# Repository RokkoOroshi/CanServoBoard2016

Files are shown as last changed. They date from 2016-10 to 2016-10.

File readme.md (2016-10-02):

# CAN Servo Driver Board

can通信機能対応サーボ制御基板

## License

- MIT

## 使用ライブラリ等

- Adafruit-PWM-Servo-Driver-Library : BSD : https://github.com/adafruit/Adafruit-PWM-Servo-Driver-Library
- CAN_BUS_Shield : MIT : https://github.com/Seeed-Studio/CAN_BUS_Shield
- MsTimer2 : LGPL : http://playground.arduino.cc/Main/MsTimer2
- pins_arduino.h : LGPL
- Arduino-SerialCommand : ? : https://github.com/kroimon/Arduino-SerialCommand

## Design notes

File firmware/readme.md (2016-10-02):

# CAN Servo Board Firmware

## Arduino IDE での使用方法
1. Arduino IDEをダウンロード・インストール
2. install.batを管理者として実行（Arduino IDEのフォルダ下に必要なファイルのシンボリックリンクを作ってる）
3. Arduino IDEのボード選択メニューで"RokkoOroshiCanServoBoard"を選択

これで各ピンのシンボルが自動で定義され、各種ライブラリをincludeできるようになる。

また、この基板はArduinoProMini互換であるが、ブートローダーは書き込み速度を通常より高速にしたものを使用しているため、IDEでArduinoProMiniを選択した場合書き込みできないので注意。

## ライブラリ
Arduino IDEのメニュー include library から選択できるようになっているはず。

現状、依存ライブラリをメインのファイル内でincludeしないとコンパイルエラーになる

### CanCommunication

* CAN上で各ノードが相互に通信するためのライブラリ
* 通信規格は独自の簡易的なものを使用、詳細はcan_communication_def.h参照
* SPI.h(標準ライブラリ), mcp_can.h(CAN_BUS_SHEILDライブラリ) に依存

## PWM出力を使う
* PWM出力は外部のIC(PCA9685)が行う
* 基本的に　https://www.switch-science.com/catalog/961/と同じ感じにしている
* Arduinoから使うライブラリが作られているので利用。使い方はそのライブラリを参照。
* サーボ用電源出力をOFFにするピンも搭載している

## IOポートを使う
* Arduino の A0,A1,A2,A3, D9,D10に当たるポートを搭載しているのでその部分はArudinoと同じように使える

## その他
* このフォルダ下にhardware_profile.h, can_communication_dfe.hがあるが、これは内容確認用に置いているだけ。RokkoOroshiCanServoBoard下の深いところに同じファイルがあり、ArduinoIDEではそちらを参照している。このフォルダ下のものは最新でない可能性があるので注意。
* ピン配置はhardware_profile.hを見ると早い
* can_communication_defには通信規格を書いている

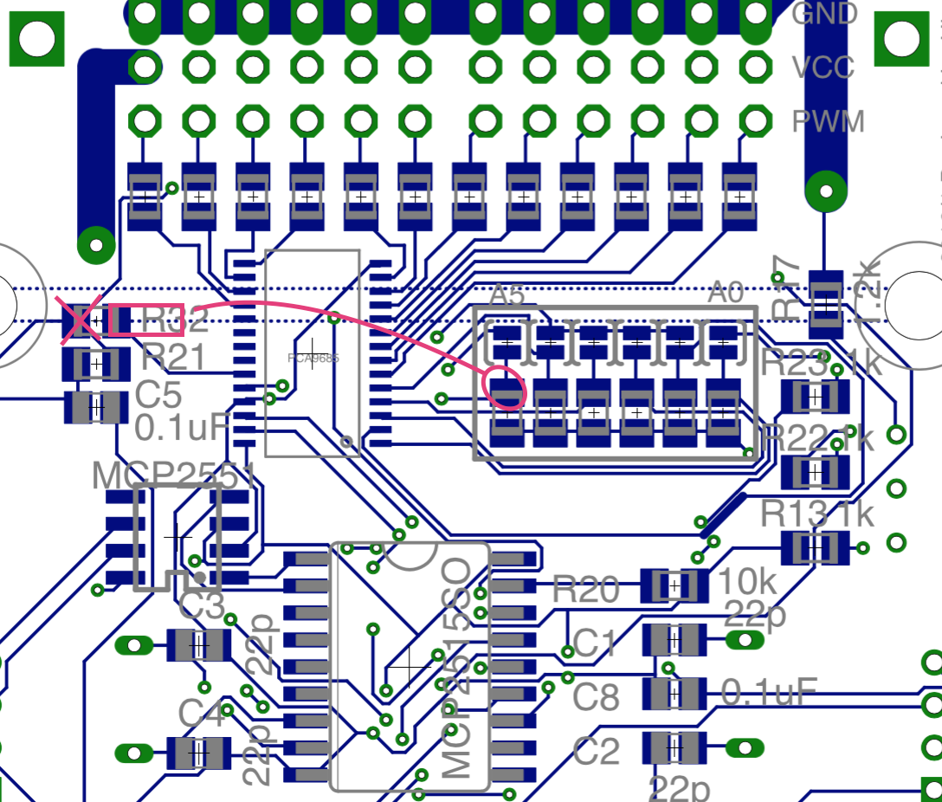
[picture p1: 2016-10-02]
hardware/基板修正箇所２.png

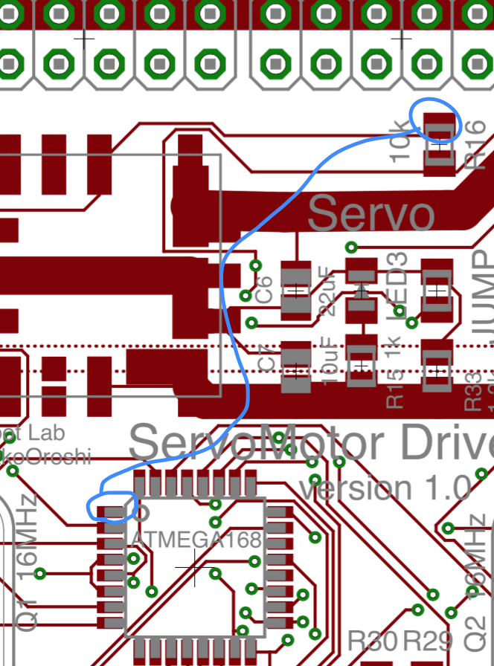
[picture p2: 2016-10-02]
hardware/基板修正箇所１.png

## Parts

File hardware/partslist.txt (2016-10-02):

抵抗

PWM出力部(R1~R12)	330Ω
白枠部(R24~R28,R31)	10kΩ

R13	1k	led
R14	1k	led
R15	1k	led
R16	10k	プルアップ
R17	1.2k	分圧
R18	可変20k
R19	39k	can
R20	10k	リセットプルアップ
R21	10k	リセットプルアップ
R22	1k	led
R23	1k	led
R29	4.7k	I2Cプルアップ
R30	4.7k	I2Cプルアップ
R32	10k
R33	1.2k

コンデンサ
C1~C4	22pF	発信子負荷
C5	0.1uF	DRT
C6	22uF
C7	10uF
C8	0.1uF	パスコン

その他
ATMega328p	1個	メインマイコン
MCP2551		1個	CAN通信
MCP2515		1個	CAN通信
水晶発信器16MHz	2個
チップLED	5個	
B2P-VH		2個	モータ、モータ電源
B4B-ZR		1個	Arduino書き込み、シリアル通信
B6B-ZR		1個	ISP書き込み
B4B-PASK	2個	CAN通信
ピンヘッダ2x3	2個	IO
ピンヘッダ3x12相当		1個	PWM

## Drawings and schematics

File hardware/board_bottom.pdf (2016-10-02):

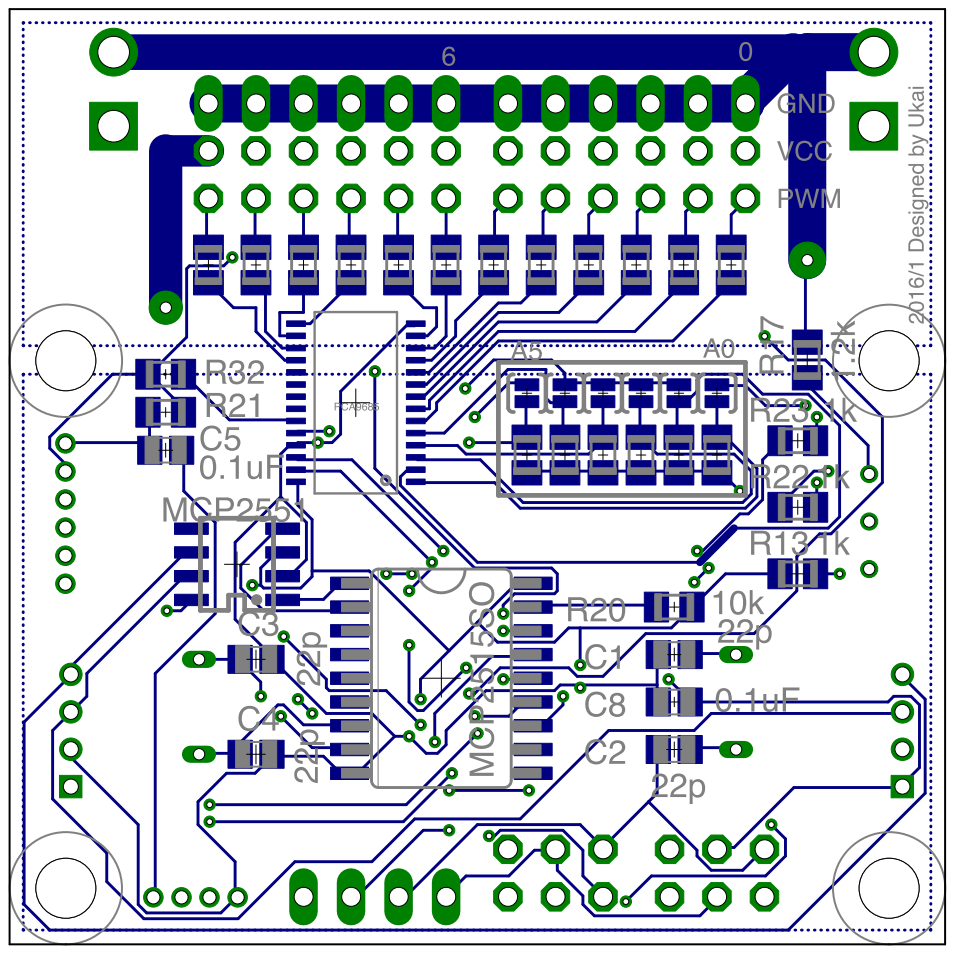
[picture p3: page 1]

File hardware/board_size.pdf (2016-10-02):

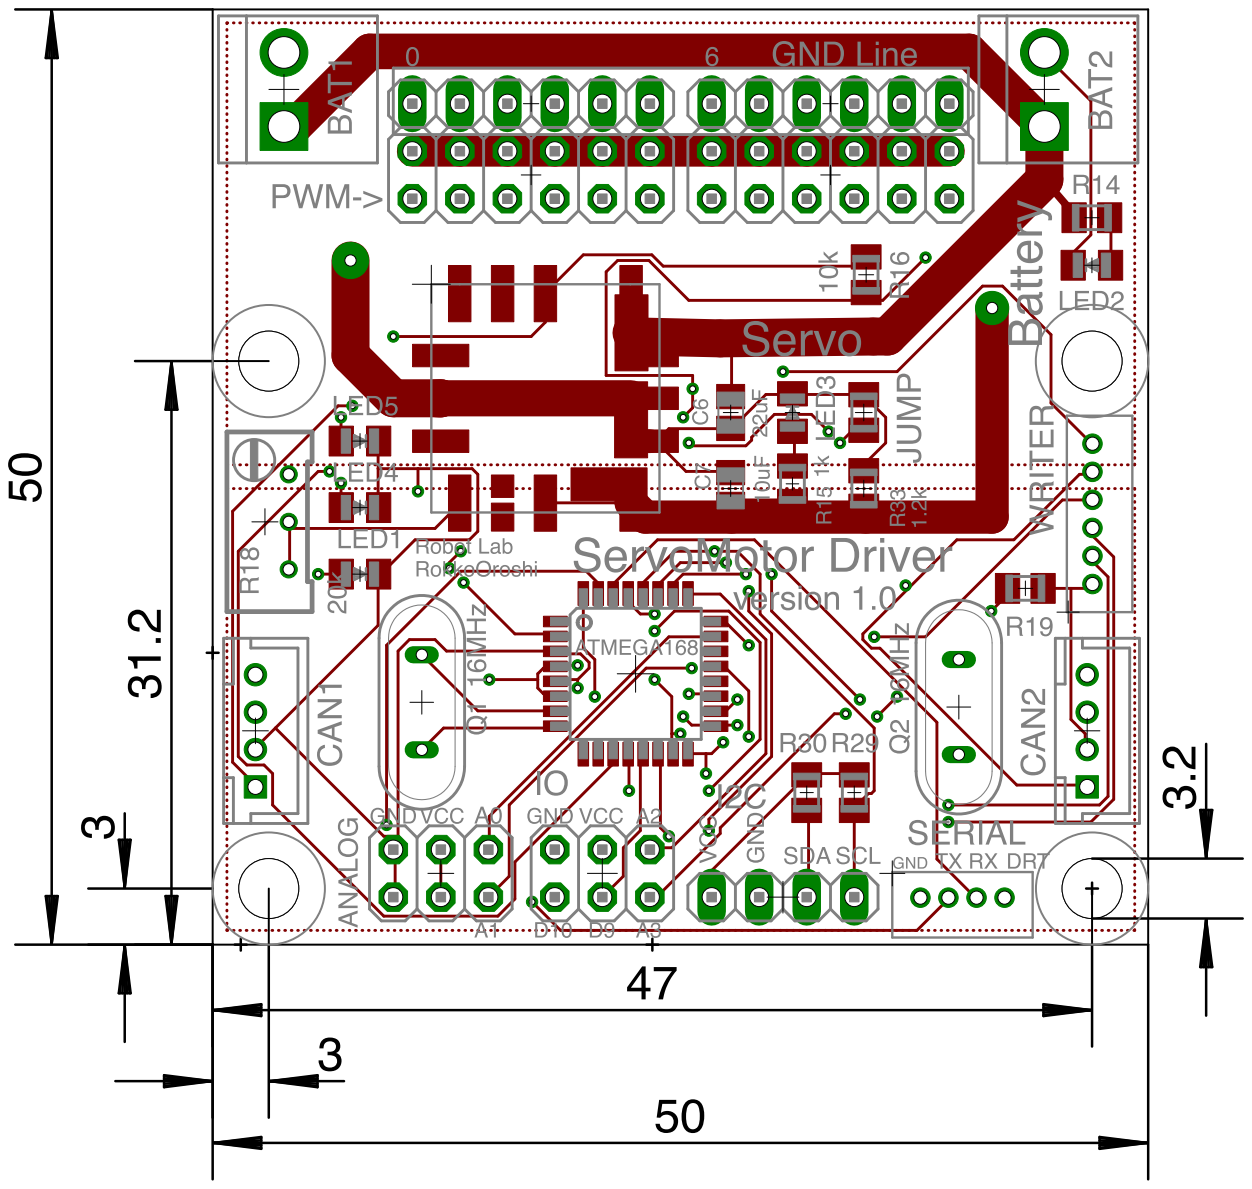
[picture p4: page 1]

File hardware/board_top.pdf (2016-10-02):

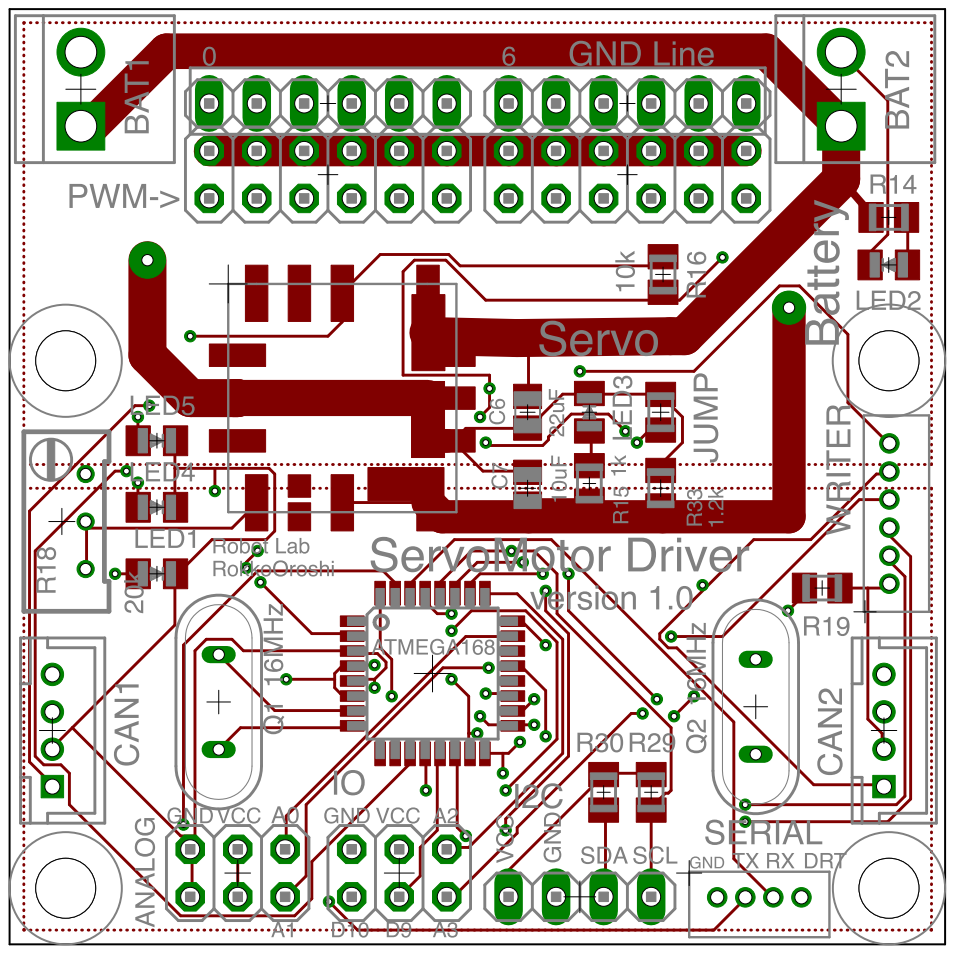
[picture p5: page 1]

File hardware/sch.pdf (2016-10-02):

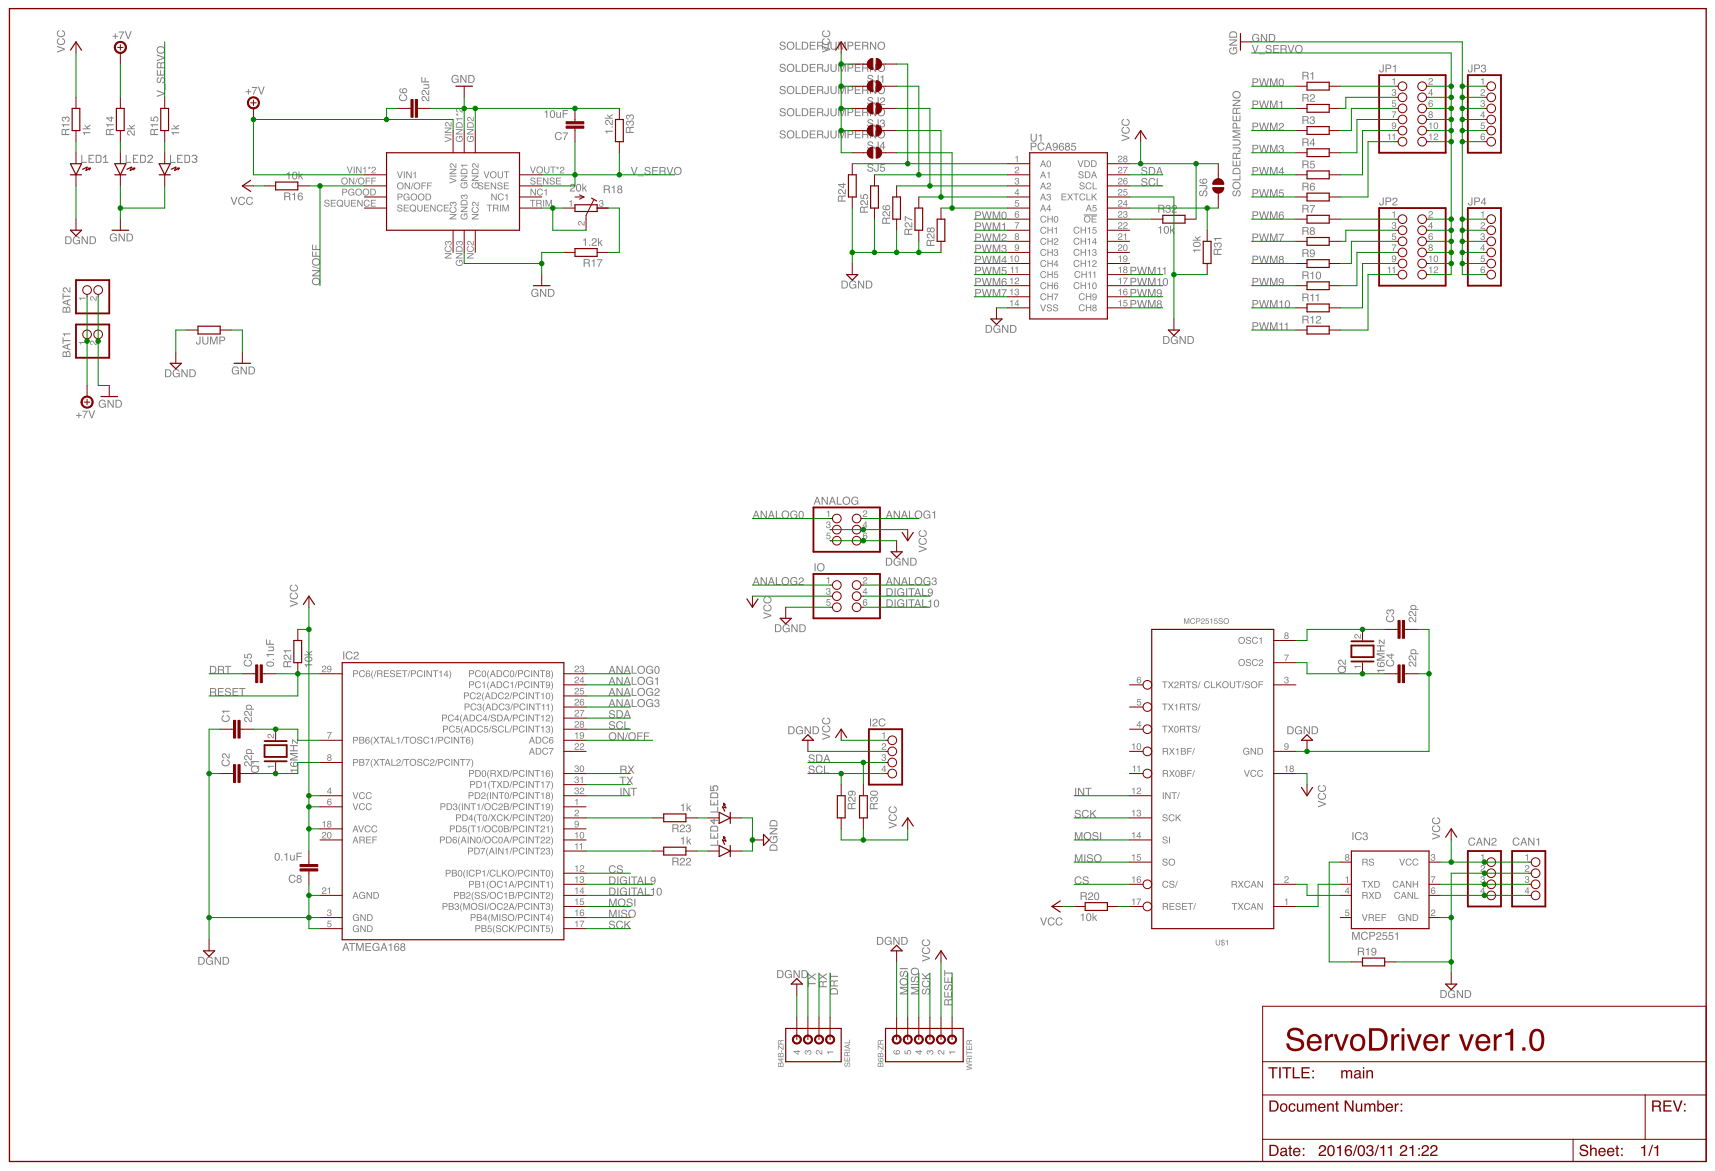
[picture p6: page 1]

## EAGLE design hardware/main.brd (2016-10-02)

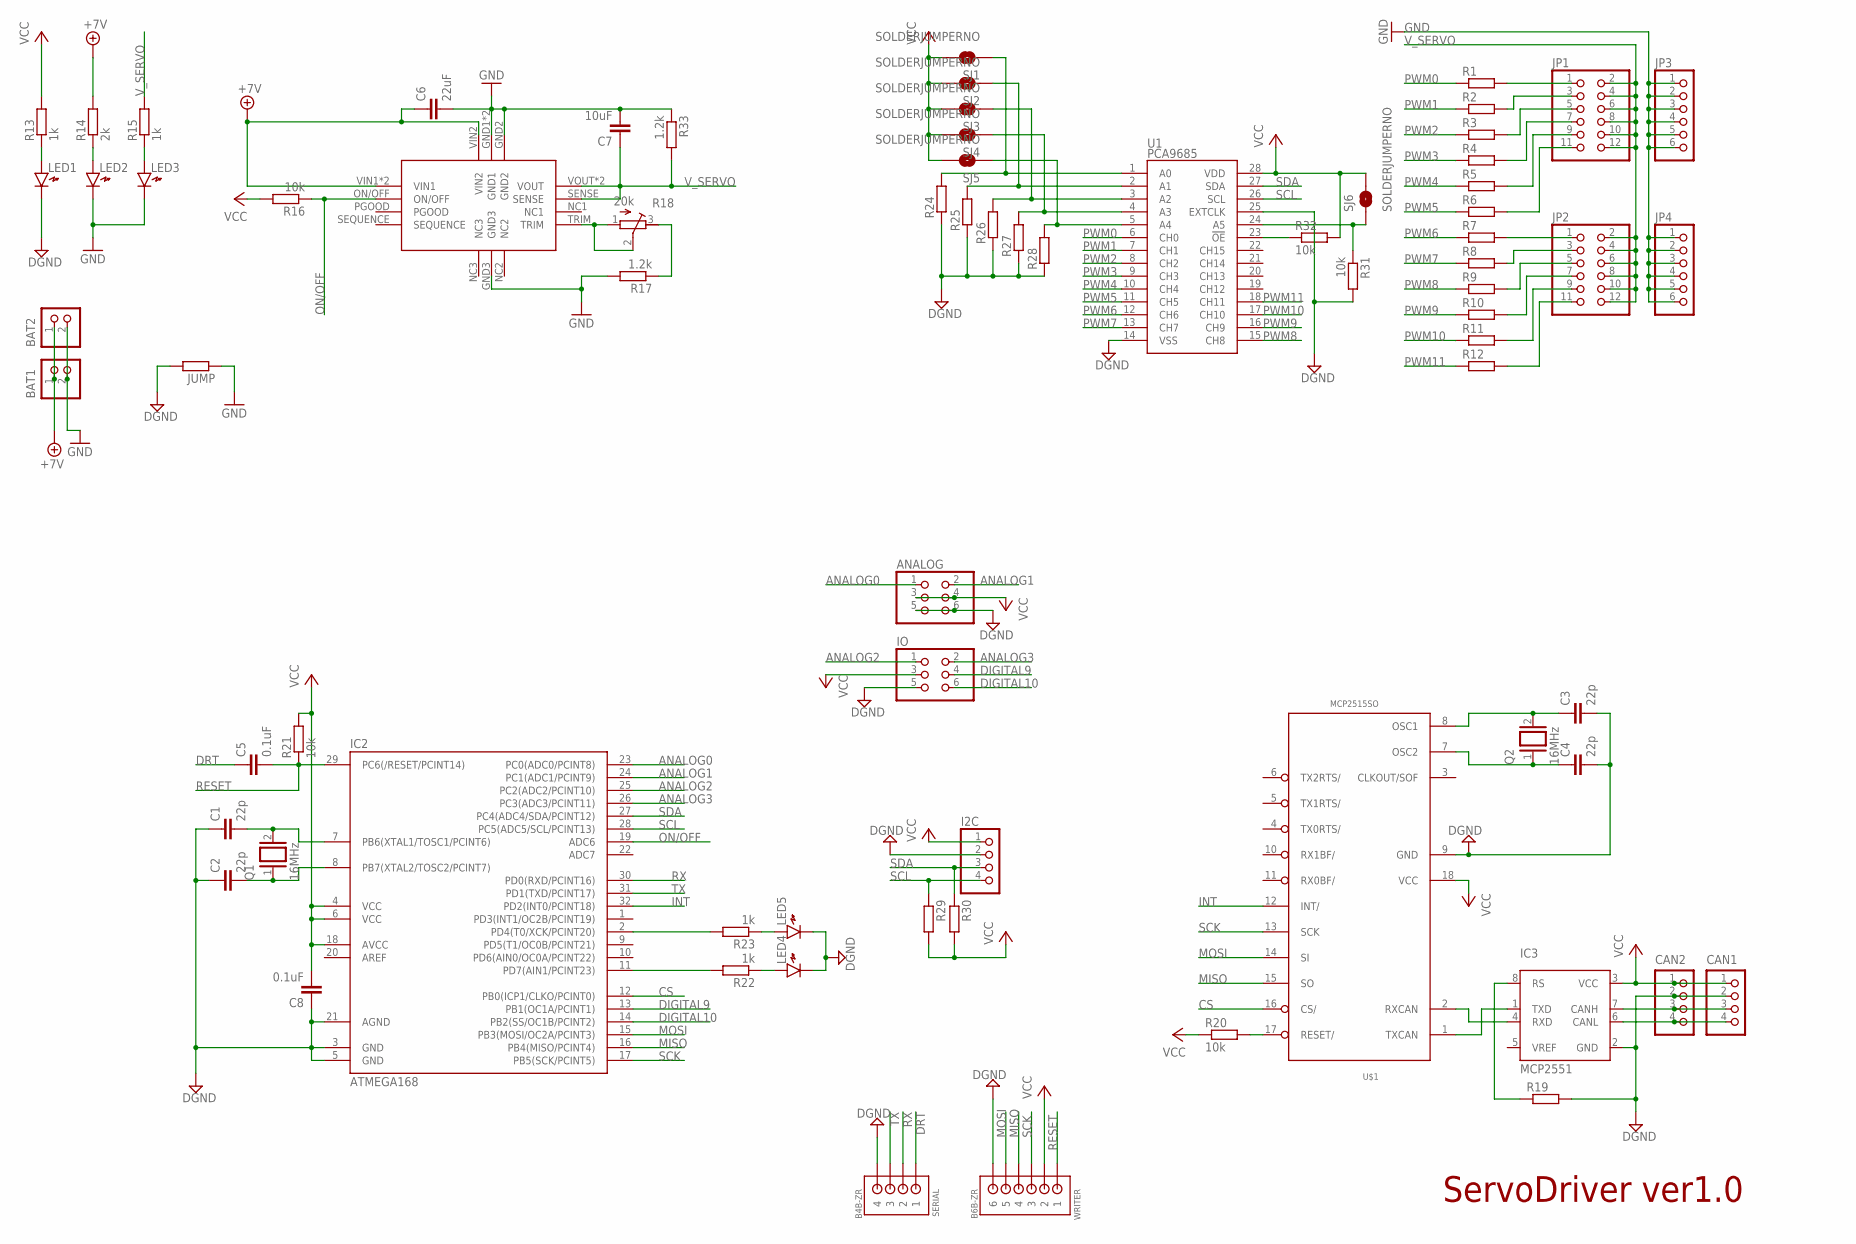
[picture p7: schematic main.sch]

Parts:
ANALOG: PINHD-2X3; 2X03
BAT1, BAT2: B2P-VH
C1, C2, C3, C4: 22p; C2012
C5, C8: 0.1uF; C2012
C6: 22uF; C2012
C7: 10uF; C2012
CAN1, CAN2: B4B-PH-K-S
I2C: PINHD-1X4; 1X04
IC1: OKL-T
IC2: ATMEGA168; TQFP32-08
IC3: MCP2551; SOIC
IO: PINHD-2X3; 2X03
JP1, JP2: PINHD-2X6; 2X06
JP3, JP4: PINHD-1X6; 1X06
JUMP: R-EU_M2012; M2012
LED1, LED2, LED3, LED4, LED5: LED2012
Q1, Q2: 16MHz; QS
R1, R2, R3, R4, R5, R6, R7, R8, R9, R10, R11, R12, R19, R24, R25, R26, R27, R28, R29, R30: R-EU_M2012; M2012
R13, R15, R22, R23: 1k; M2012
R14: 2k; M2012
R16, R20, R21, R31, R32: 10k; M2012
R17, R33: 1.2k; M2012
R18: 20k; RTRIM64W
SERIAL: B4B-ZR
SJ1, SJ2, SJ3, SJ4, SJ5, SJ6: SOLDERJUMPERNO; SJ_2S-NO
U1: PCA9685; TSSOP-28_4MM
U$1: MCP2515SO; SO18L
WRITER: B6B-ZR

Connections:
+7V: BAT1.1, BAT2.1, C6.1, IC1.VIN1, IC1.VIN2, IC1.VIN_BRIDGE (VIN1), R14.2
ANALOG0: ANALOG.1, IC2.23 (PC0(ADC0/PCINT8))
ANALOG1: ANALOG.2, IC2.24 (PC1(ADC1/PCINT9))
ANALOG2: IC2.25 (PC2(ADC2/PCINT10)), IO.1
ANALOG3: IC2.26 (PC3(ADC3/PCINT11)), IO.2
CS: IC2.12 (PB0(ICP1/CLKO/PCINT0)), U$1.16 (CS/)
DGND: ANALOG.5, ANALOG.6, C1.1, C2.1, C3.2, C4.2, C8.1, CAN1.2, CAN2.2, I2C.2, IC2.3 (GND), IC2.5 (GND), IC2.21 (AGND), IC3.2 (GND), IO.5, JUMP.2, LED1.K, LED4.K, LED5.K, R19.2, R24.1, R25.1, R26.1, R27.1, R28.1, R31.2, SERIAL.4, U1.14 (VSS), U1.25 (EXTCLK), U$1.9 (GND), WRITER.6
DIGITAL9: IC2.13 (PB1(OC1A/PCINT1)), IO.4
DIGITAL10: IC2.14 (PB2(SS/OC1B/PCINT2)), IO.6
DRT: C5.1, SERIAL.1
GND: BAT1.2, BAT2.2, C6.2, C7.2, IC1.GND1, IC1.GND2, IC1.GND3, IC1.GND_BRIDGE (GND1), JP3.1, JP3.2, JP3.3, JP3.4, JP3.5, JP3.6, JP4.1, JP4.2, JP4.3, JP4.4, JP4.5, JP4.6, JUMP.1, LED2.K, LED3.K, R17.2, R33.1
INT: IC2.32 (PD2(INT0/PCINT18)), U$1.12 (INT/)
MISO: IC2.16 (PB4(MISO/PCINT4)), U$1.15 (SO), WRITER.4
MOSI: IC2.15 (PB3(MOSI/OC2A/PCINT3)), U$1.14 (SI), WRITER.5
unnamed: JP1.1, R1.2
unnamed: JP1.3, R2.2
unnamed: JP1.5, R3.2
unnamed: JP1.7, R4.2
unnamed: JP1.9, R5.2
unnamed: JP1.11, R6.2
unnamed: JP2.1, R7.2
unnamed: JP2.3, R8.2
unnamed: JP2.5, R9.2
unnamed: JP2.7, R10.2
unnamed: JP2.9, R11.2
unnamed: JP2.11, R12.2
unnamed: LED1.A, R13.1
unnamed: LED2.A, R14.1
unnamed: LED3.A, R15.1
unnamed: IC1.TRIM, R18.1 (A), R18.2 (S)
unnamed: R17.1, R18.3 (E)
unnamed: C2.2, IC2.8 (PB7(XTAL2/TOSC2/PCINT7)), Q1.1
unnamed: R24.2, SJ1.1, U1.1 (A0)
unnamed: C1.2, IC2.7 (PB6(XTAL1/TOSC1/PCINT6)), Q1.2
unnamed: IC3.1 (TXD), U$1.1 (TXCAN)
unnamed: IC3.4 (RXD), U$1.2 (RXCAN)
unnamed: IC3.8 (RS), R19.1
unnamed: CAN1.3, CAN2.3, IC3.7 (CANH)
unnamed: CAN1.4, CAN2.4, IC3.6 (CANL)
unnamed: C4.1, Q2.1, U$1.7 (OSC2)
unnamed: C3.1, Q2.2, U$1.8 (OSC1)
unnamed: R25.2, SJ2.1, U1.2 (A1)
unnamed: R26.2, SJ3.1, U1.3 (A2)
unnamed: R27.2, SJ4.1, U1.4 (A3)
unnamed: IC2.2 (PD4(T0/XCK/PCINT20)), R23.2
unnamed: R28.2, SJ5.1, U1.5 (A4)
unnamed: R32.1, U1.23 (!OE)
unnamed: R20.2, U$1.17 (RESET/)
unnamed: IC2.11 (PD7(AIN1/PCINT23)), R22.2
unnamed: LED4.A, R22.1
unnamed: LED5.A, R23.1
unnamed: R31.1, SJ6.1, U1.24 (A5)
ON/OFF: IC1.ON/OFF, IC2.19 (ADC6), R16.1
PWM0: R1.1, U1.6 (CH0)
PWM1: R2.1, U1.7 (CH1)
PWM2: R3.1, U1.8 (CH2)
PWM3: R4.1, U1.9 (CH3)
PWM4: R5.1, U1.10 (CH4)
PWM5: R6.1, U1.11 (CH5)
PWM6: R7.1, U1.12 (CH6)
PWM7: R8.1, U1.13 (CH7)
PWM8: R9.1, U1.15 (CH8)
PWM9: R10.1, U1.16 (CH9)
PWM10: R11.1, U1.17 (CH10)
PWM11: R12.1, U1.18 (CH11)
RESET: C5.2, IC2.29 (PC6(/RESET/PCINT14)), R21.1, WRITER.1
RX: IC2.30 (PD0(RXD/PCINT16)), SERIAL.2
SCK: IC2.17 (PB5(SCK/PCINT5)), U$1.13 (SCK), WRITER.3
SCL: I2C.4, IC2.28 (PC5(ADC5/SCL/PCINT13)), R29.1, U1.26 (SCL)
SDA: I2C.3, IC2.27 (PC4(ADC4/SDA/PCINT12)), R30.1, U1.27 (SDA)
TX: IC2.31 (PD1(TXD/PCINT17)), SERIAL.3
VCC: ANALOG.3, ANALOG.4, C8.2, CAN1.1, CAN2.1, I2C.1, IC2.4 (VCC), IC2.6 (VCC), IC2.18 (AVCC), IC3.3 (VCC), IO.3, R13.2, R16.2, R20.1, R21.2, R29.2, R30.2, R32.2, SJ1.2, SJ2.2, SJ3.2, SJ4.2, SJ5.2, SJ6.2, U1.28 (VDD), U$1.18 (VCC), WRITER.2
V_SERVO: C7.1, IC1.SENSE, IC1.VOUT, IC1.VOUT_BRIDGE (VOUT), JP1.2, JP1.4, JP1.6, JP1.8, JP1.10, JP1.12, JP2.2, JP2.4, JP2.6, JP2.8, JP2.10, JP2.12, R15.2, R33.2

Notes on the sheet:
ServoDriver ver1.0

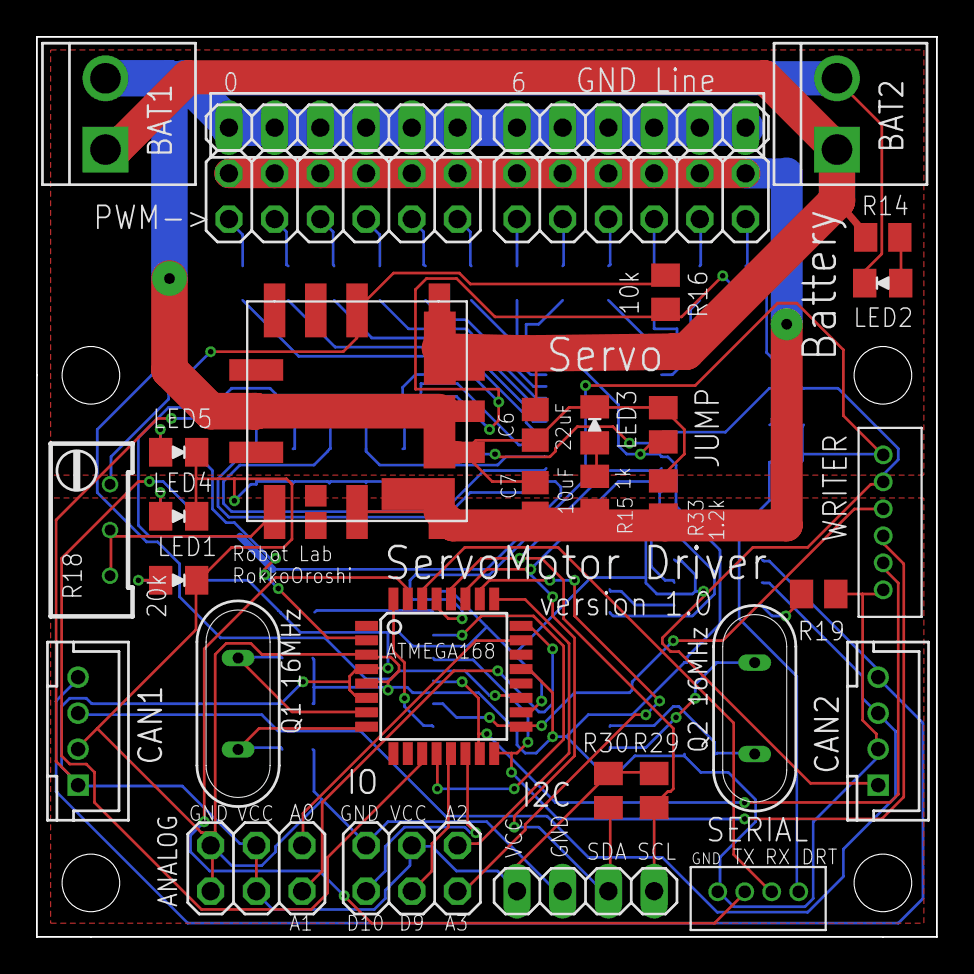
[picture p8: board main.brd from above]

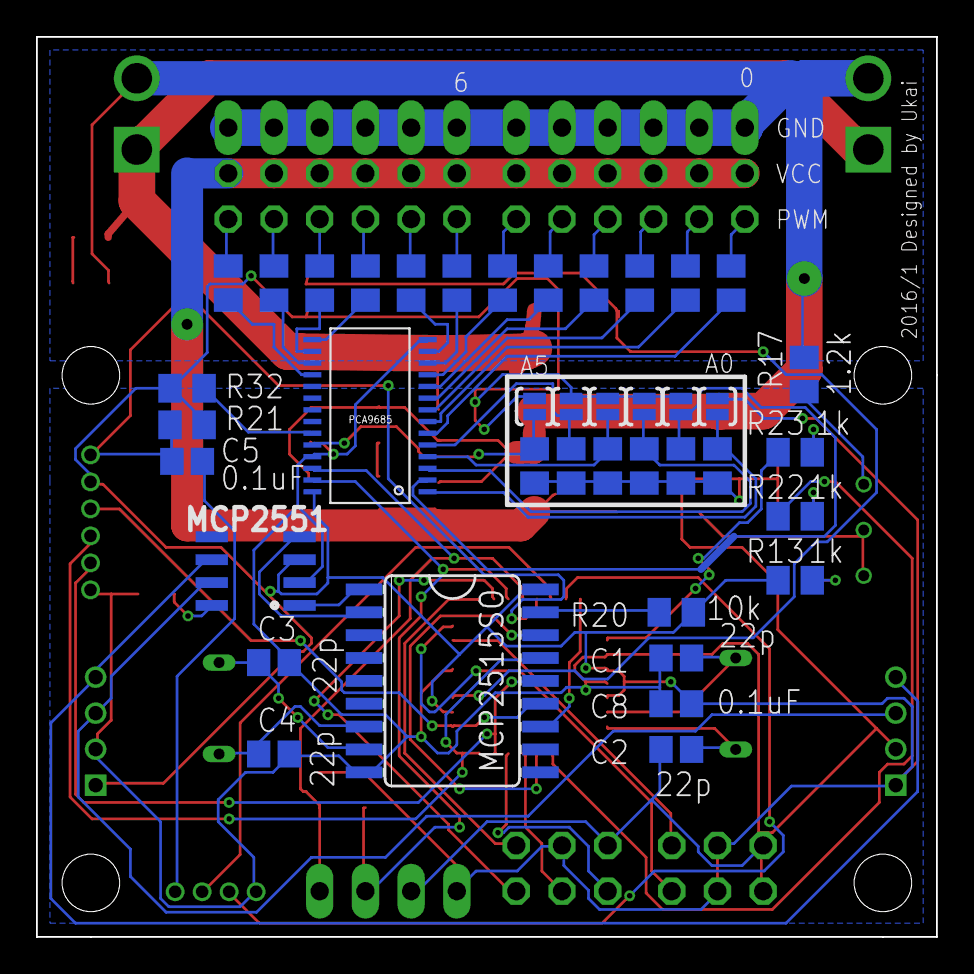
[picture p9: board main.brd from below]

Board: 2 copper layers, 50.0 x 50.0 mm, 73 parts (40 on the bottom side), 73 nets.

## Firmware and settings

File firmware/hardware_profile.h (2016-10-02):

#ifndef HARDWARE_PROFILE_H
#define HARDWARE_PROFILE_H

/*
  Arduino - AVR
  ---------
  D0  - PD0
  D1  - PD1
  D2  - PD2
  D3  - PD3
  D4  - PD4
  D5  - PD5
  D6  - PD6
  D7  - PD7
  ---------
  D8  - PB0
  D9  - PB1
  D10 - PB2
  D11 - PB3
  D12 - PB4
  D13 - PB5
  ---------
  A0  - PC0
  A1  - PC1
  A2  - PC2
  A3  - PC3
  A4  - PC4
  A5  - PC5
  (32pin Only)
  A6  - ADC6
  A7  - ADC7
 */


// Digital Pin
static const uint8_t SPI_CS   =  8;
static const uint8_t SPI_MOSI = 11;
static const uint8_t SPI_MISO = 12;
static const uint8_t SPI_SCK  = 13;

static const uint8_t CAN_INT  =  2;
static const uint8_t CAN_CS   =  8;
static const uint8_t CAN_MOSI = 11;
static const uint8_t CAN_MISO = 12;
static const uint8_t CAN_SCK  = 13;

static const uint8_t RX       =  0;
static const uint8_t TX       =  1;

static const uint8_t STAT_LED1=  4;
static const uint8_t STAT_LED2=  7;


static const uint8_t SERVO_OFF = 3;

// Analog Pin
static const uint8_t INPUT0 = 14; // A0
static const uint8_t INPUT1 = 15; // A1
static const uint8_t INPUT2 = 16; // A2
static const uint8_t INPUT3 = 17; // A3

static const uint8_t INPUT9 = 9; // D9
static const uint8_t INPUT10 = 10;// D10

static const uint8_t I2C_SDA = 18; // A4
static const uint8_t I2C_SCL = 19;  // A5

#endif

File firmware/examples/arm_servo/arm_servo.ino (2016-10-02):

/**
 * author : Kenya Ukai
 * license: MIT
 *
 */

#include<Wire.h>
#include<Adafruit_PWMServoDriver.h>

#include <avr/wdt.h>
#include <SPI.h>
#include <mcp_can.h>
#include <SerialCommand.h>
#include <can_communication.h>
#include <can_communication_def.h>


Adafruit_PWMServoDriver pwm = Adafruit_PWMServoDriver();


enum CAN_COMMAND {
    CAN_COMMAND_RESET = 0,
    CAN_COMMAND_ARM = 1,
    CAN_COMMAND_CAMERA = 2
};

const uint8_t ARM_TOP = 0;
const uint8_t ARM_MIDDLE = 2;
const uint8_t ARM_BOTTOM = 3;
const uint8_t CAM_TOP = 4;
const uint8_t CAM_BOTTOM = 5;

const double SERVO_MAX_PULSE_WIDTH[] = {2.0, 2.0, 1.8, 2.0, 2.0, 2.0};
const double SERVO_MIN_PULSE_WIDTH[] = {0.5, 0.5, 0.5, 0.5, 0.5, 0.5};

const uint8_t CAN_SPEED     = CAN_250KBPS;
const uint8_t TPIP_CAN_ADDR = 1;
const uint8_t self_can_addr = 8;

SerialCommand SCmd;
uint32_t timer_cnt;
bool connection_alive;

unsigned long prev_01;
unsigned long prev_1;

void setup() {
    Serial.begin(115200);

    pinMode(STAT_LED1, OUTPUT);
    pinMode(STAT_LED2, OUTPUT);
    pinMode(SERVO_OFF, OUTPUT);
    digitalWrite(SERVO_OFF, LOW);
    CanCom.begin(self_can_addr, CAN_SPEED);
    CanCom.onReceive(canOnReceive);

    pwm.begin();
    pwm.setPWMFreq(50); // 20ms
    
    Serial.println("Arm Servo Program");
    Serial.print("addr : ");
    Serial.println(self_can_addr);

    Serial.println("* Commands : ");
    Serial.println("* <top | middle | bottom> <-90 ~ 90>");
    Serial.println("* <s 0 ~ 10> <-90 ~ 90>");
    
    SCmd.addCommand("t", topCallback);
    SCmd.addCommand("m", middleCallback);
    SCmd.addCommand("b", bottomCallback);
    SCmd.addCommand("s", servoCallback);
    
    Serial.println(". . . Ready !");

    for (int i = 0; i < 10; i++) {
        setServoAngle(i, 1.5);
    }
    
    wdt_enable(WDTO_120MS);
}

//
// CAN通信
//

static void canOnReceive(uint16_t std_id, const byte* data, uint8_t len) {
    uint8_t type = CanCommunication::getDataTypeFromStdId(std_id);
    uint8_t src  = CanCommunication::getSrcFromStdId(std_id);
    uint8_t dest = CanCommunication::getDestFromStdId(std_id);

    digitalWrite(STAT_LED2, !digitalRead(STAT_LED2));
    
    if(dest != self_can_addr) return;
    
    if (type == CAN_DATA_TYPE_COMMAND) {
        connection_alive = true;
        
        switch (data[0]) {
            case CAN_COMMAND_RESET:
                if(len == 2) {
                    uint8_t reset = data[1];
                    digitalWrite(SERVO_OFF, reset);
                }
            case CAN_COMMAND_ARM:
                if(len == 1 + 3) {
                    int8_t top = CanCommunication::get<int8_t>(&data[1]);
                    int8_t middle = CanCommunication::get<int8_t>(&data[2]);
                    int8_t bottom = CanCommunication::get<int8_t>(&data[3]);
                    setServoAngle(ARM_TOP, top);
                    setServoAngle(ARM_MIDDLE, middle);
                    setServoAngle(ARM_BOTTOM, bottom);
                }
                break;
            case CAN_COMMAND_CAMERA:
                if(len == 1 + 2) {
                    int8_t top = CanCommunication::get<int8_t>(&data[1]);
                    int8_t bottom = CanCommunication::get<int8_t>(&data[2]);
                    setServoAngle(CAM_TOP, top);
                    setServoAngle(CAM_BOTTOM, bottom);
                }
            default:
                break;
        }
    }
}

static void topCallback() {
    const char *arg = SCmd.next();
    if(arg == NULL) {
        parseError();
        return;
    }
    int16_t pos = atoi(arg);
    if(abs(pos) > 90) pos = 90 * (pos > 0 ? 1 : -1);
    setServoAngle(ARM_TOP, pos);
    /*
    uint8_t data[1] = { CAN_COMMAND_ARM_MOTOR };
    CanCommunication::set<int8_t>(&data[1], (int8_t)speed);
    canOnReceive(
        CanCommunication::generateStdId(CAN_DATA_TYPE_COMMAND,
                                        self_can_addr,
                                        self_can_addr),
        data, 2);
    */
        
}
static void middleCallback() {
    const char *arg = SCmd.next();
    if(arg == NULL) {
        parseError();
        return;
    }
    int16_t pos = atoi(arg);
    if(abs(pos) > 90) pos = 90 * (pos > 0 ? 1 : -1);
    setServoAngle(ARM_MIDDLE, pos);
}
static void bottomCallback() {
    const char *arg = SCmd.next();
    if(arg == NULL) {
        parseError();
        return;
    }
    int16_t pos = atoi(arg);
    if(abs(pos) > 90) pos = 90 * (pos > 0 ? 1 : -1);
    setServoAngle(ARM_BOTTOM, pos);
}

void servoCallback() {
    const char *arg = SCmd.next();
    if(arg == NULL) {
        parseError();
        return;
    }
    int num = atoi(arg);
    if(num < 0 || num >= 12) return;
    arg = SCmd.next();
    if(arg == NULL) {
        parseError();
        return;
    }
    int angle = atoi(arg);    
    if(abs(angle) > 90) angle = 90 * (angle > 0 ? 1 : -1);
    setServoAngle(num, angle);
}

void parseError() { Serial.println("parse error"); }

//
// その他
//

void loop() {
    SCmd.readSerial();
    CanCom.tasks();

    unsigned long now = millis();
    if(now - prev_01 >= 100) {
        wdt_reset();
        if (!connection_alive) {
        } else {
            connection_alive = false;
        }
        prev_01 = now;
    }
    if(now - prev_1 >= 1000) {
        digitalWrite(STAT_LED1, !digitalRead(STAT_LED1));
        CanCom.sendHeartBeat();
        prev_1 = now;
    }
}

void setServoAngle(uint8_t n, double deg) {
    if(deg < -90) deg = -90;
    if(deg > 90) deg = 90;
    double width = SERVO_MAX_PULSE_WIDTH[n] - SERVO_MIN_PULSE_WIDTH[n];
    double pulse = (deg + 90) / 180 * width + SERVO_MIN_PULSE_WIDTH[n];
    setServoPulse(n, pulse);
}

// pulse : ms
void setServoPulse(uint8_t n, double pulse) {
  double pulselength;
  
  pulselength = 1000000;   // 1,000,000 us per second
  pulselength /= 60;   // 60 Hz
  Serial.print(pulselength); Serial.println(" us per period"); 
  pulselength /= 4096;  // 12 bits of resolution
  Serial.print(pulselength); Serial.println(" us per bit"); 
  pulse *= 1000;
  pulse /= pulselength;
  Serial.println(pulse);
  pwm.setPWM(n, 0, pulse);
}

//ウォッチドッグタイマー用おまじない
uint8_t mcusr_mirror __attribute__((section(".noinit")));
void get_mcusr(void) __attribute__((naked)) __attribute__((section(".init3")));
void get_mcusr(void) {
    mcusr_mirror = MCUSR;
    MCUSR = 0;
    wdt_disable();
}

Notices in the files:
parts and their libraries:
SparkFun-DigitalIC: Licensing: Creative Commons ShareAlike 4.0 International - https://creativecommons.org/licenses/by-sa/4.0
